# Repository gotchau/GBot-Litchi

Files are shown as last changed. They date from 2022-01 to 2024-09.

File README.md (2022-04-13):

# 3D принтер GBot Litchi

<a href="https://discord.gg/KYU2nGtZ2r" style="height: 40px !important;">Join us on Discord</a>

**⚠ Данный принтер находится в разработке. Детали могут изменится в любой момент. Скачивая и изготовливая их сейчас, вы делаете это на свой страх и риск. Промежуточный дизайн опубликован по многочисленным просьбам и для людей, которые не против принять участие в β-тесте.**

Это принтер с областью печати 180³мм³. Рама максимально универсальная и позволяет собирать принтер на нескольких кинематиках:
  * Hbot
  * CoreXY\*
  * GBot Sync\*\*
  * GBot Type A/C/D\*\*\*
  * IDEX\*\*\*\*

И сразу пару сносок:  
\* *под CoreXY детали в разработке, однако рама достаточно жесткая, **рекомендуемая кинематика — Hbot.***  
\*\* *GBot Sync — смесь HBot и Makerbot, где от Makerbot стоит пассивная ось Y, которая является синхронизатором и не допускает перекоса балки, присущего HBot'ам.*  
\*\*\* *автор собирает на GBot Type A, подробнее можно узнать тут [в этом видео про кинематики].*  
\*\*\*\* *IDEX гипотетически поддерживается, требуется растянуть раму по оси X.*  

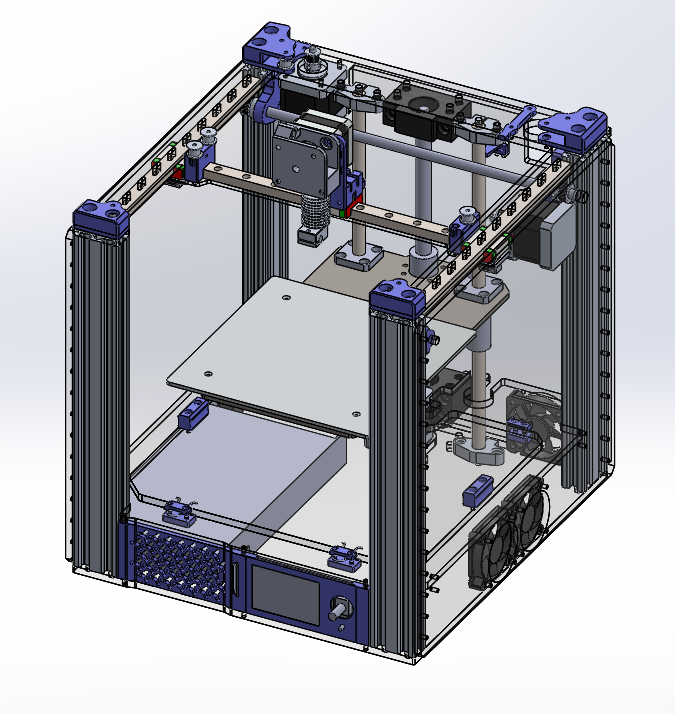
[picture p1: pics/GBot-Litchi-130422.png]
Внешний вид принтер


## Обзор конструкции
Основная часть рамы состоит из шести деталей: двух акриловых пластин и четырех профилей v-слот 2040. Профили стоят перпендикулярно и повышают жесткость и способность рамы сопротивляться скручиванию. Однако этого недостаточно, поэтому по бокам и сзади принтер тоже обшит акрилом. Боковые стенки в идеале брать толщиной 4мм (выйдет достаточно жестко и не так дорого). Автор использует везде акрил 6мм.

[в этом видео про кинематики]: https://youtu.be/pnqFbjBa5Ig

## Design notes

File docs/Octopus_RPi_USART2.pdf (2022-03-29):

### Подключение Raspberry Pi3b+ к Octopus v1.1 через USART2

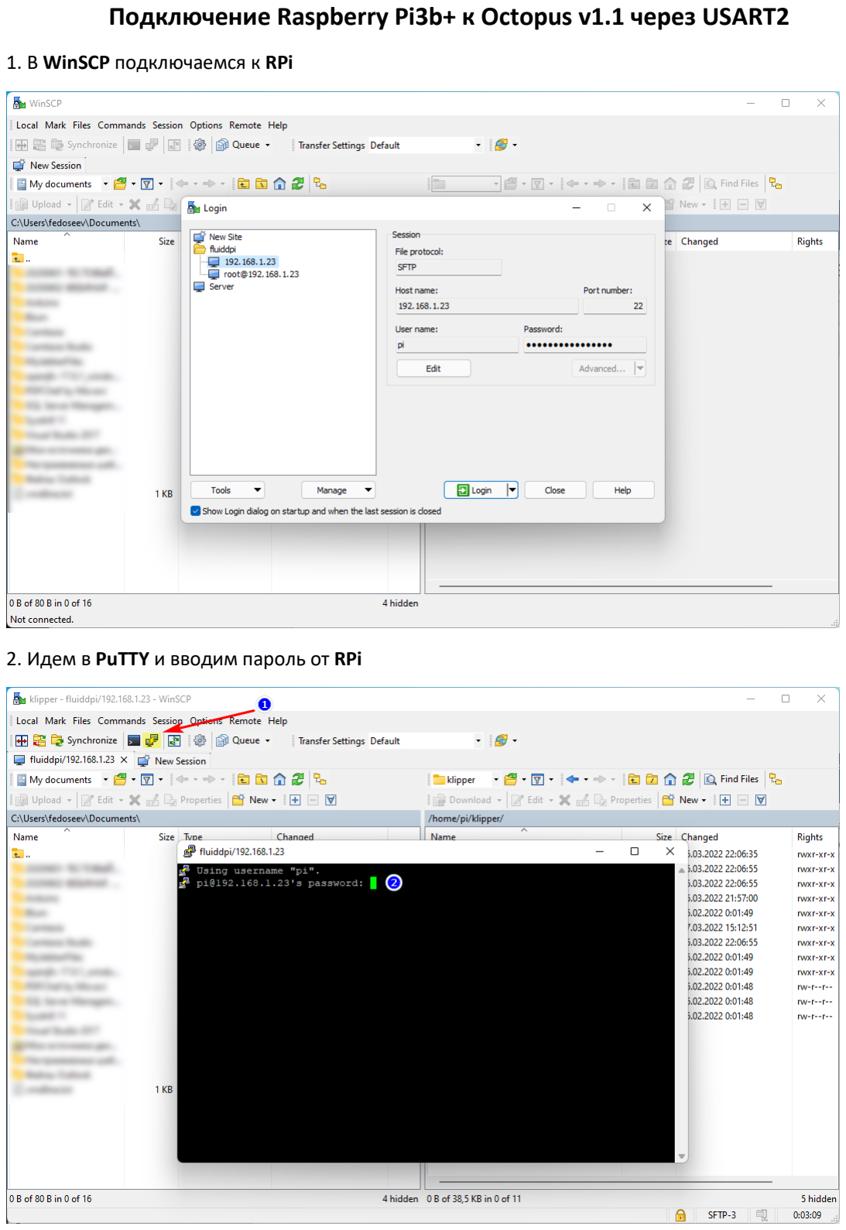
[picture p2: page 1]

1. В WinSCP подключаемся к RPi
2. Идем в PuTTY и вводим пароль от RPi

3. Переходим в папку klipper (1): cd ~/klipper и затем пишем команду make menuconfig
4. Необходимые параметры для платы BTT Octopus v1.1 (446)
a) Micro-controller Architecture (STMicroelectronics STM32)
b) Processor model (STM32F446)
c) Bootloader offset (32KiB bootloader)
d) Clock Reference (12 MHz crystal)
e) Communication interface (Serial (on USART2 PD6/PD5)) <- только для подключения через USART2
f) (250000) Baud rate for serial port

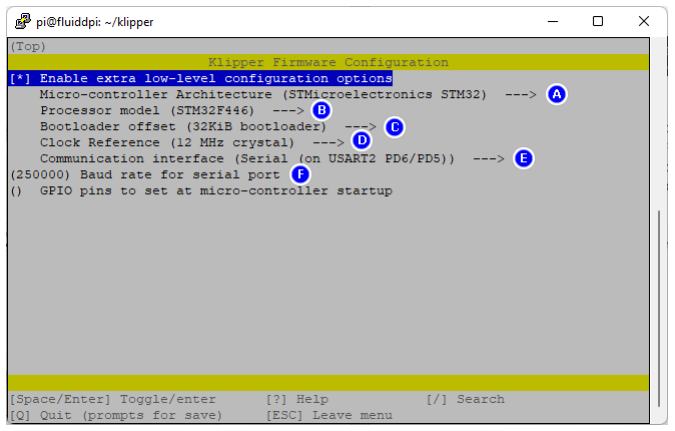
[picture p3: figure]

5. Нажимаем Q и сохраняем.
6. Пишем команду make и ждем пока создается прошивка. Файл пошивки klipper.bin можно найти в папке /home/pi/klipper/out.

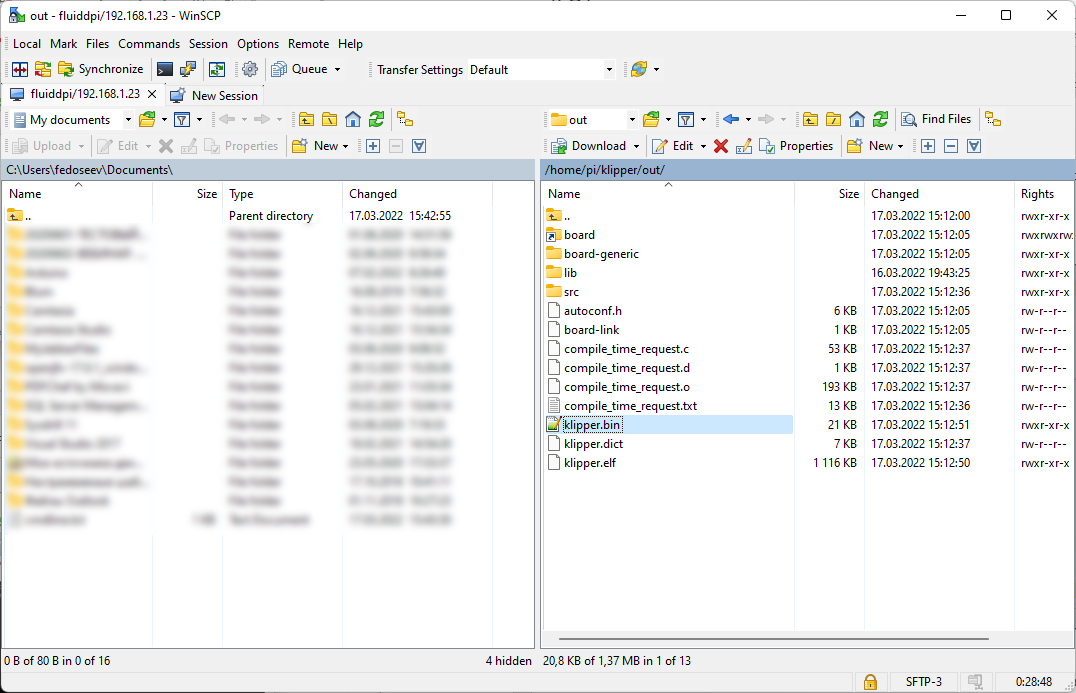
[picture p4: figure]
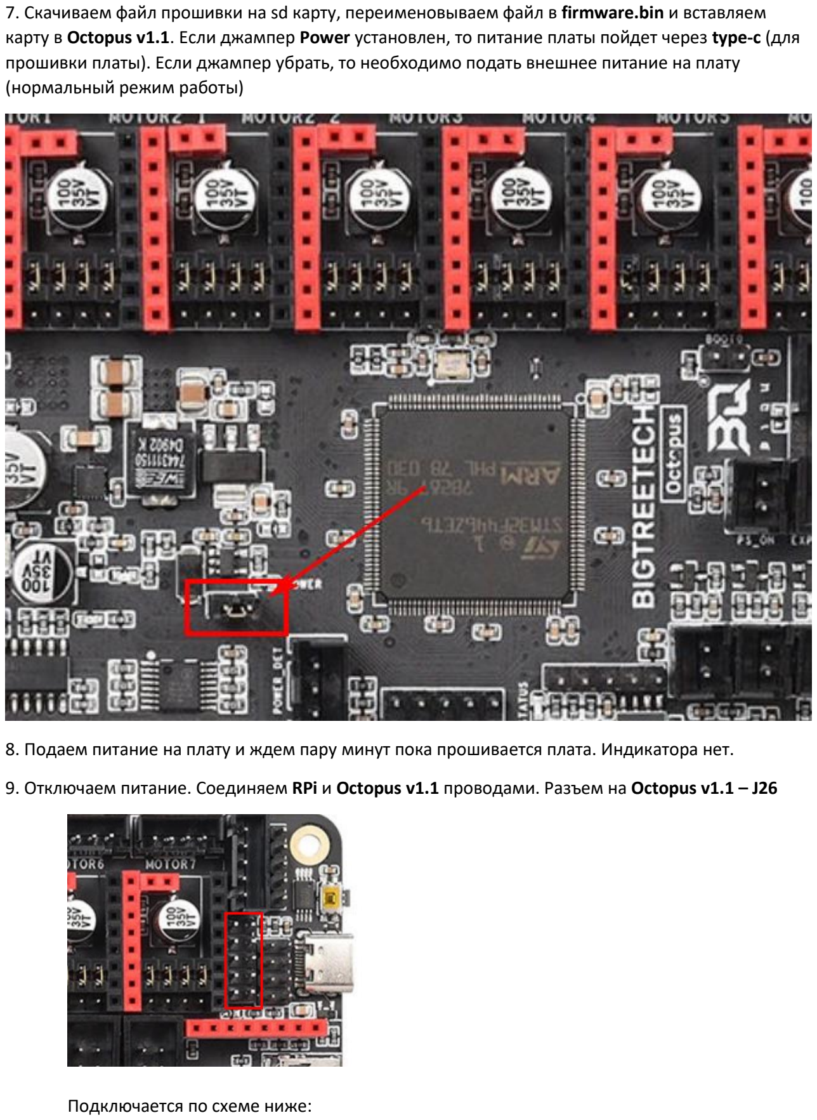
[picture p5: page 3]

7. Скачиваем файл прошивки на sd карту, переименовываем файл в firmware.bin и вставляем карту в Octopus v1.1. Если джампер Power установлен, то питание платы пойдет через type-c (для прошивки платы). Если джампер убрать, то необходимо подать внешнее питание на плату (нормальный режим работы)
8. Подаем питание на плату и ждем пару минут пока прошивается плата. Индикатора нет.
9. Отключаем питание. Соединяем RPi и Octopus v1.1 проводами. Разъем на Octopus v1.1 – J26

Подключается по схеме ниже:

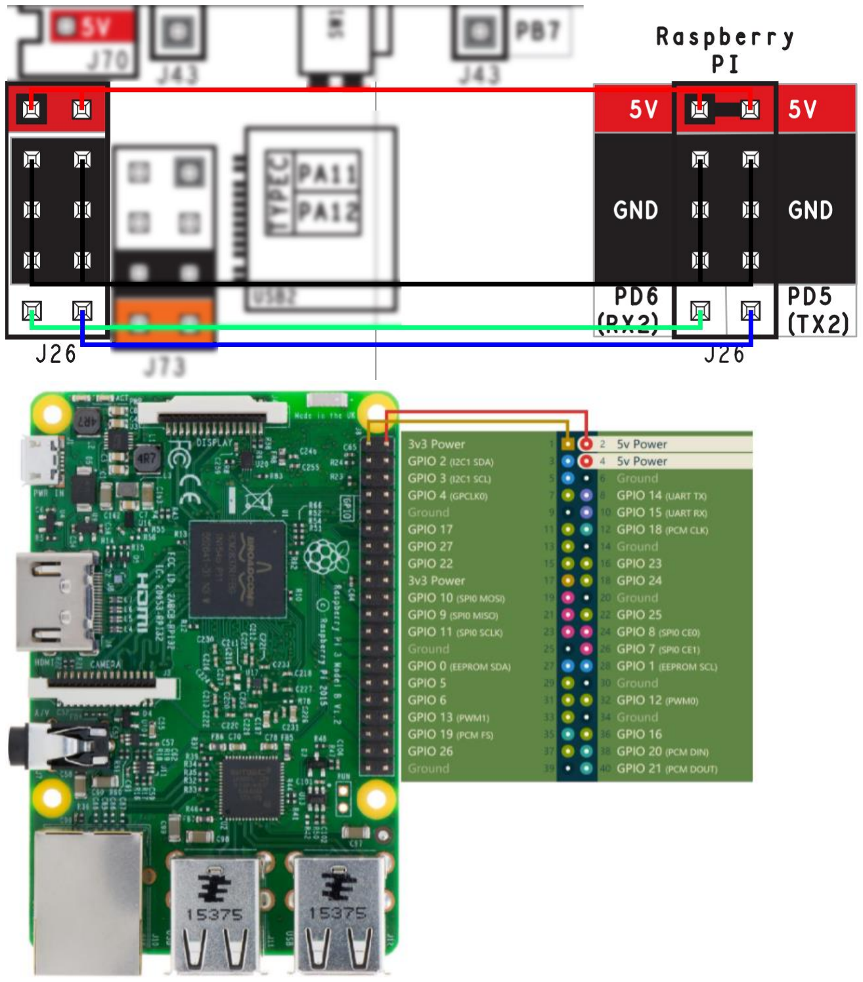
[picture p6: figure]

Плата Octopus v1.1 | RPi 3B+
5V | 5v Power
5V | 5v Power
GND | Ground
GND | Ground
PD6 (RX2) | GPIO 14 (UART TX)
PD5 (TX2) | GPIO 15 (UART RX)

Должно получиться так:

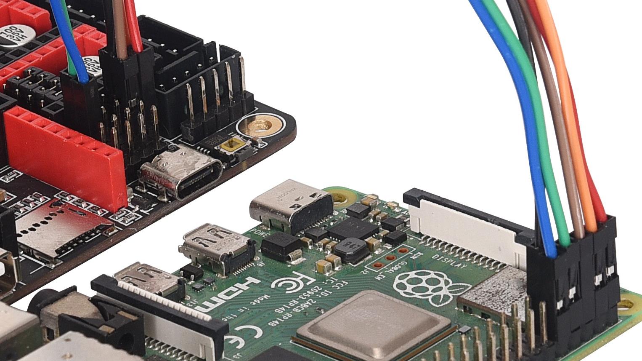
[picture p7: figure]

10. Подаем питание на Octopus (джампер Power снят, питание внешнее).
11. Заходим через WinSCP с правами root на RPi, идем сюда /boot/cmdline.txt и удаляем console=serial0,115200
12. Добавляем dtoverlay=pi3-miniuart-bt в конец файла /boot/config.txt
13. В файле конфигурации printer.cfg модифицируем раздел [mcu]

[mcu]
serial: /dev/ttyAMA0
restart_method: command
14. Перезагружаемся.

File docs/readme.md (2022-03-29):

Здесь будут публиковаться документация по принтеру:
* Основной мануал (в разработке)
* Даташиты на электронные компоненты, применяемые в принтере
* Мануалы по отдельным вариативным этапам сборки

Принять активное участие по разработке принтера можно в нашем **дискорд сервере**:  
https://discord.gg/KYU2nGtZ2r

Список файлов с пояснением:

* **A3141-2-3-4-Datasheet.pdf** -> даташит на датчик Холла A3144, применяемый в качестве концевика

* **Octopus_RPi_USART2.pdf** -> подключение RaspberryPi к Octopus  
За данную поэтапную инструкцию огромная благодарность art#9748

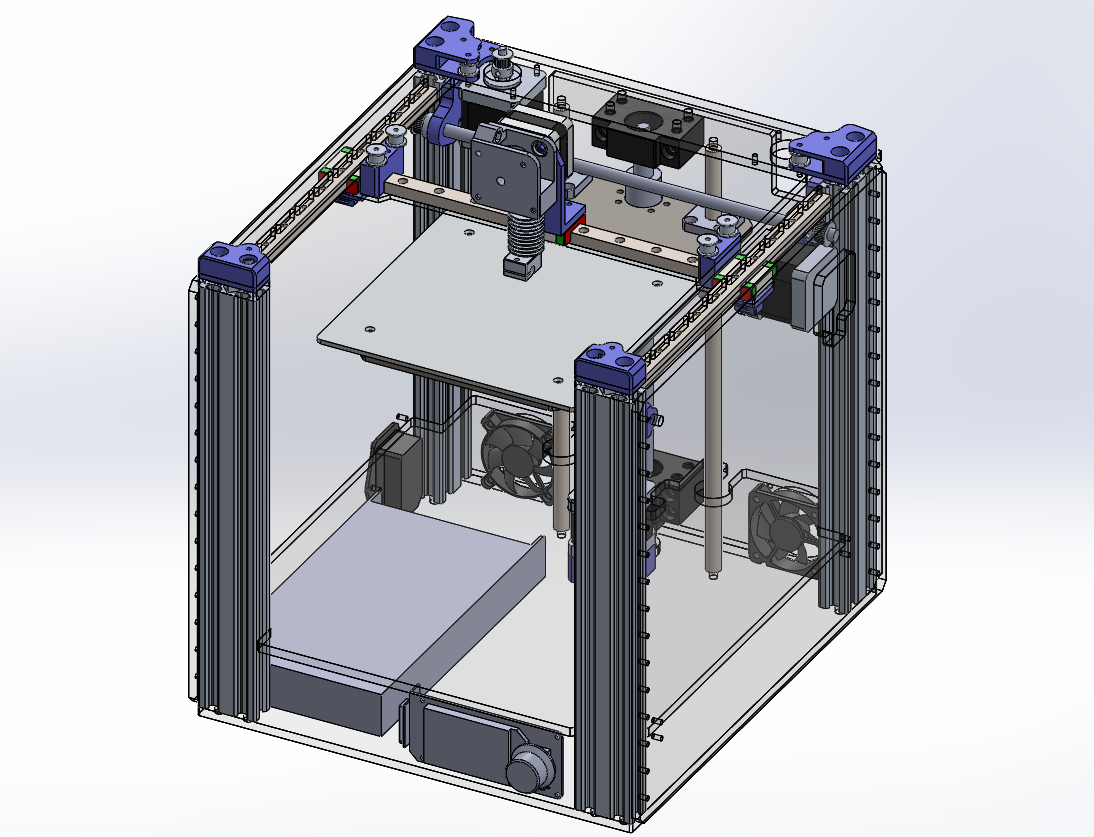
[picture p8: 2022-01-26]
pics/early-rough-design.png

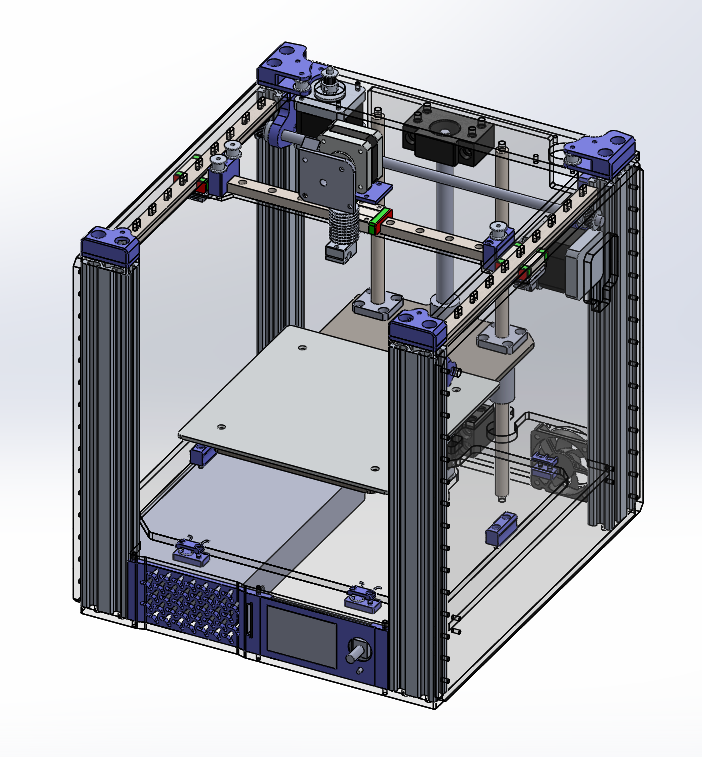
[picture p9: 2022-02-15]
pics/GBot-Litchi-150222.png

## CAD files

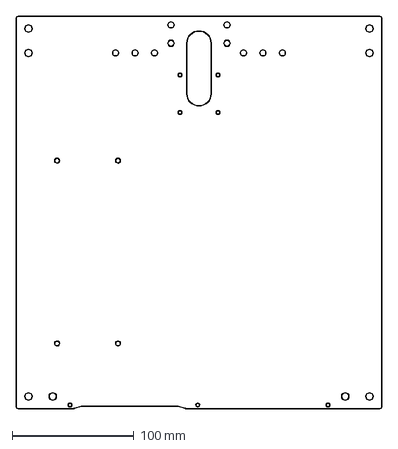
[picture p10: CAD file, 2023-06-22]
CAD/DXF/bottomPlate GBtLitchi.DXF
300.0 x 322.0 mm

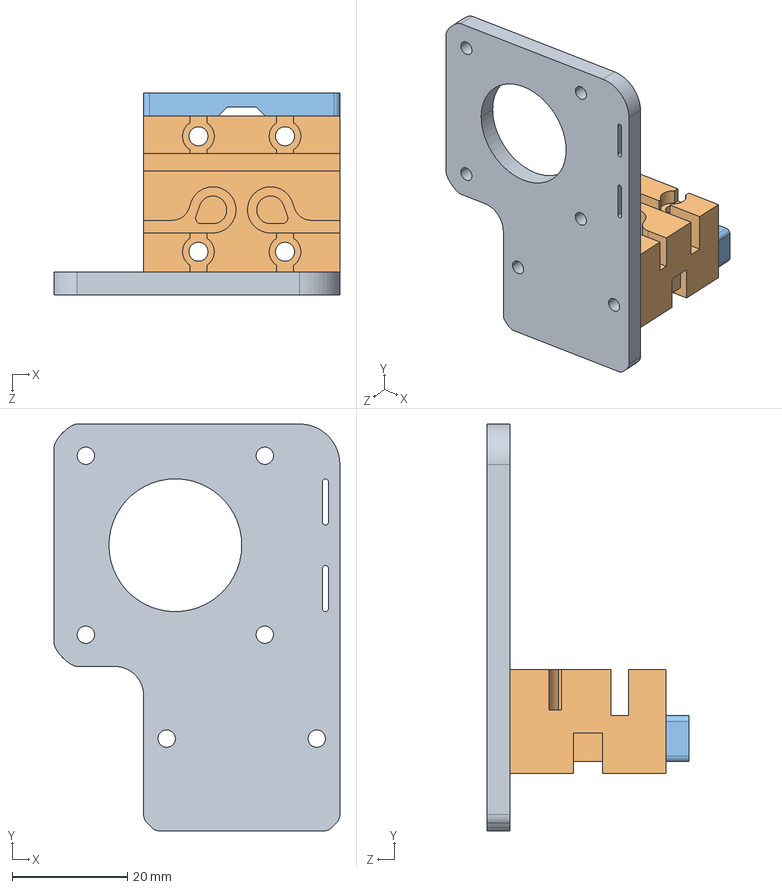
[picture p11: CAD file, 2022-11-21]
CAD/STEP/extruderMount Mk2 GBtLitchi.STEP
49.5 x 70.5 x 35.0 mm

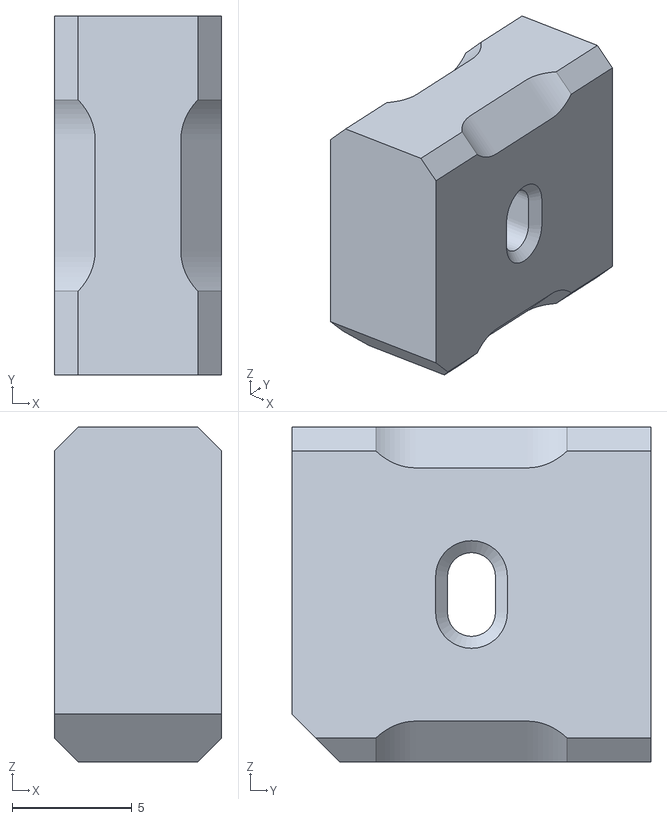
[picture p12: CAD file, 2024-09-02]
CAD/STL/zHallEndstopMount GBtLitchiMII.STL
7.00 x 15.0 x 14.0

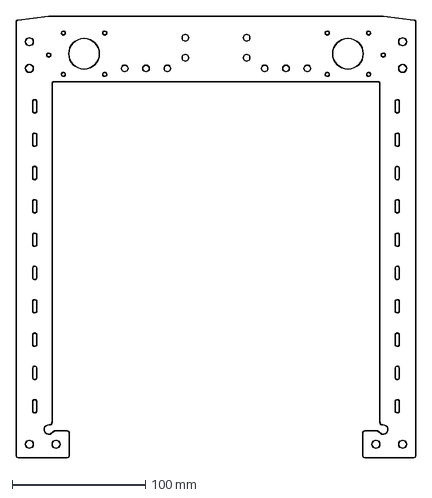
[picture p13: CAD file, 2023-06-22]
CAD/DXF/topPlate GBtLitchi.DXF
300.0 x 331.0 mm

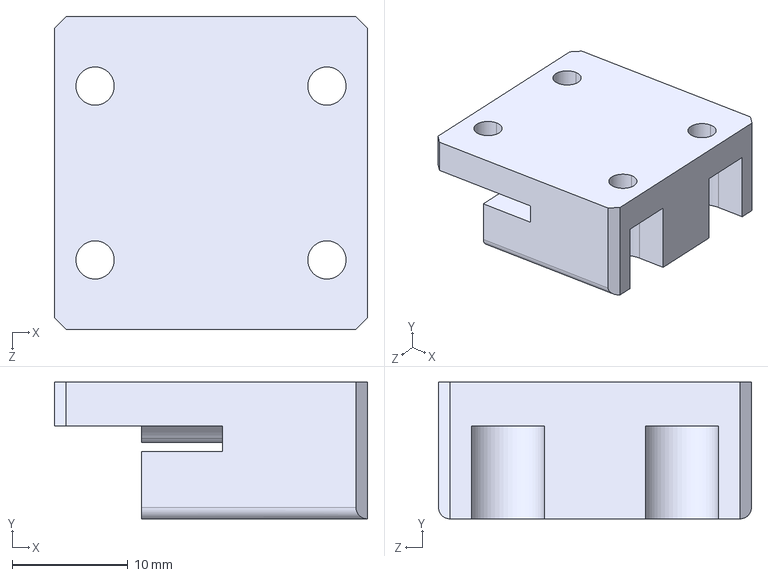
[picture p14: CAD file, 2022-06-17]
CAD/STEP/yBeltClip Mk2 T2 GBtLitchi.STEP
27.0 x 11.8 x 27.0 mm

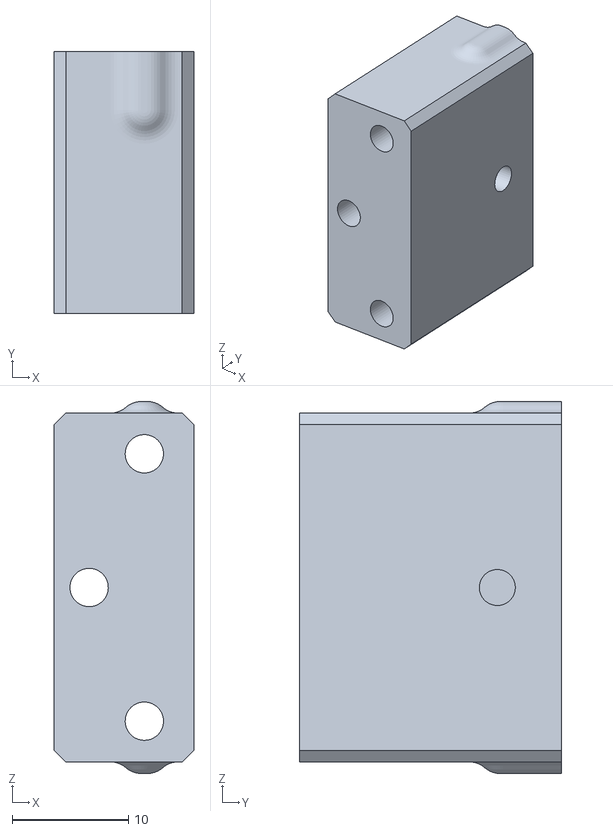
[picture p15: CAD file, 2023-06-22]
CAD/STL/rollersMount GBtLitchi.STL
12.0 x 22.5 x 32.0

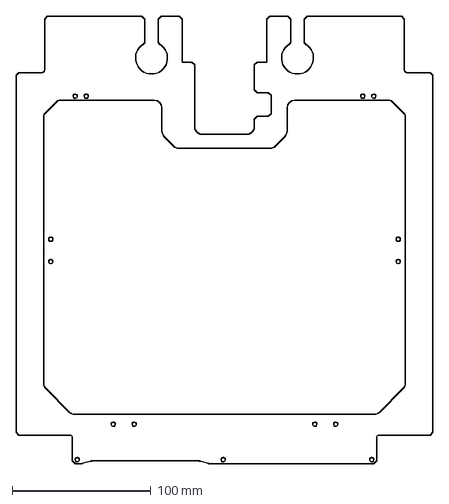
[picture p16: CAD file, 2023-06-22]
CAD/DXF/electronicsCover GBtLitchi.DXF
300.0 x 322.0 mm

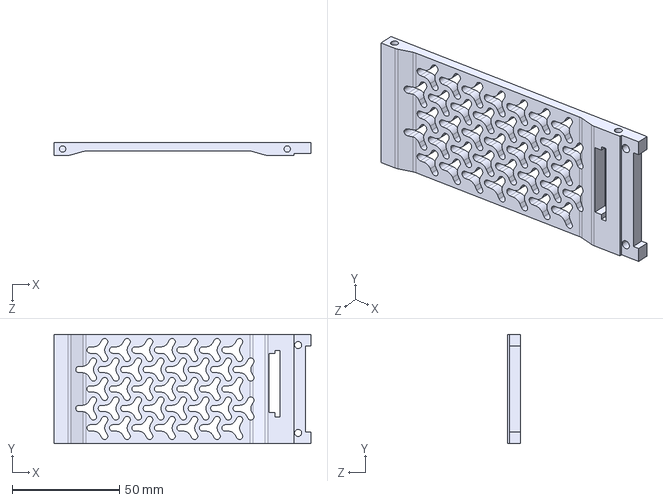
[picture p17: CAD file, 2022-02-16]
CAD/STEP/leftMini12864PanelMount GBtLitchi.STEP
120.0 x 51.0 x 6.00 mm

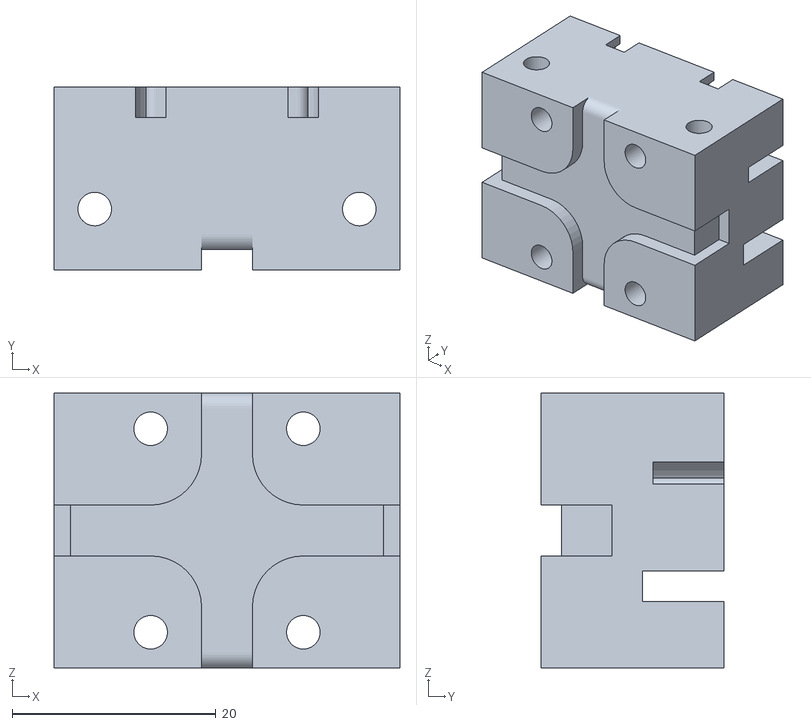
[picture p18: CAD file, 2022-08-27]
CAD/STL/extruderMount Mk2 P1 GBtLitchi.STL
34.0 x 18.0 x 27.0

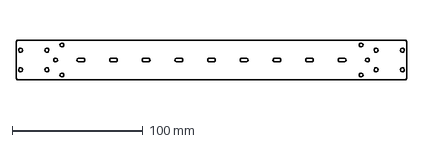
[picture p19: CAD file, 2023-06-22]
CAD/DXF/xRailSupport GBtLitchi.DXF
299.0 x 30.0 mm

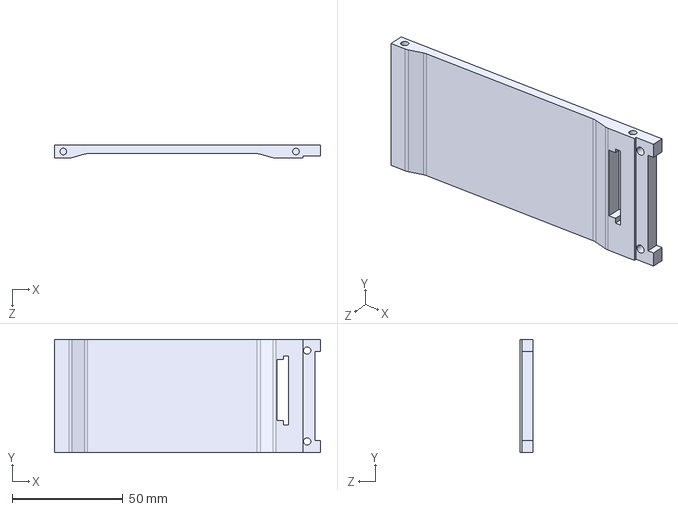
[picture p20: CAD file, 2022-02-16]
CAD/STEP/leftMini12864PanelMount Blank GBtLitchi.STEP
120.0 x 51.0 x 6.00 mm

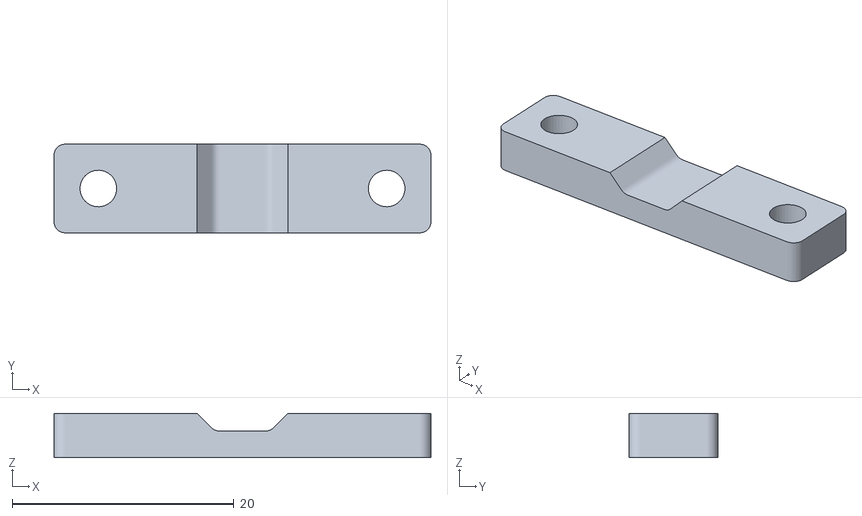
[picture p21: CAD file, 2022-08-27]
CAD/STL/extruderMount Mk2 P3 GBtLitchi.STL
34.0 x 8.00 x 4.00

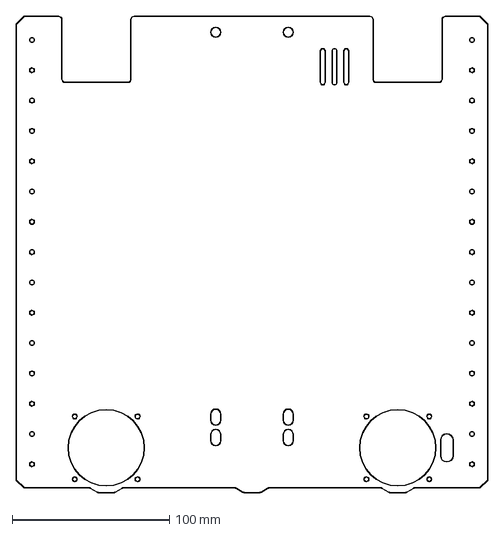
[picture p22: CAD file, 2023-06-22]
CAD/DXF/backPanel GBtLitchi.DXF
300.0 x 303.0 mm

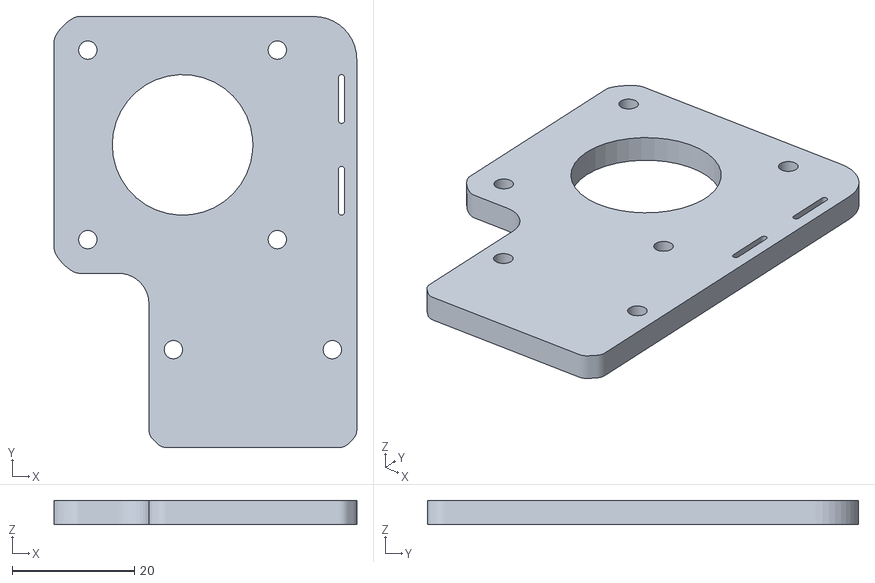
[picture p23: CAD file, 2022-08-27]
CAD/STL/extruderMount Mk2 P2 GBtLitchi.STL
49.5 x 70.5 x 4.00

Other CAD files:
CAD/DXF/leftPanel GBtLitchi.DXF
CAD/STL/stepperIdlePulleyMount I GBtLitchi.STL
CAD/DXF/rightPanel GBtLitchi.DXF
CAD/STL/hexStandoff3mm.STL
CAD/DXF/extruderMount Mk2 GBtLitchi.DXF
CAD/DXF/hotbedMount GBtLitchi.DXF
CAD/STL/extruderMount GBtLitchi.STL
CAD/STL/extruderMount II GBtLitchi.STL
CAD/STL/frontIdlePulleyMount GBtLitchi.STL
CAD/STL/frontIdlePulleyNut.STL
CAD/STL/hexStandoffRaspberry.STL
CAD/STL/idlePulleyMount I GBtLitchi.STL
CAD/STL/idlePulleyMount II GBtLitchi.STL
CAD/STL/justOneNut.STL
CAD/STL/leftMini12864PanelMount Blank GBtLitchi.STL
CAD/STL/leftMini12864PanelMount GBtLitchi.STL
CAD/STL/nutCap.STL
CAD/STL/panelProfileNutX3 sup.STL
CAD/STL/panelProfileNutX3.STL
CAD/STL/stepperIdlePulleyMount II GBtLitchi.STL
CAD/STL/yBeltClip Mk2 T2 GBtLitchi.STL
CAD/STL/yBeltClip.STL
CAD/STL/yDriveNut.STL
CAD/STL/yDriveRodMount Motor.STL
CAD/STL/yDriveRodMount.STL
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

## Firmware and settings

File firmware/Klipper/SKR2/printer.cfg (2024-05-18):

#Конфигурационный файл GBot Litchi
#Плата BTT SKR 2
#Кинематика GBot TypeA (Markforged)
#Gotchau 23.03.22

[stepper_x]
step_pin: PE2
dir_pin: PE1
enable_pin: !PE3
microsteps: 16
rotation_distance: 32
endstop_pin: ^!PC1
position_endstop: 180
position_max: 180
homing_speed: 50
homing_positive_dir: true
homing_retract_dist: 2

[stepper_y]
step_pin: PD5
dir_pin: PD4
enable_pin: !PD6
microsteps: 16
rotation_distance: 40
endstop_pin: ^!PC3
position_endstop: 180
position_max: 180
homing_speed: 50
#homing_positive_dir: true
homing_retract_dist: 2

[stepper_z]
step_pin: PA15
dir_pin: !PA8
enable_pin: !PD1
microsteps: 16
rotation_distance: 4
endstop_pin: ^!PC0
position_min: 0.0
position_max: 166.5
#position_endstop = 0
homing_speed: 10

[extruder]
step_pin: PD15
dir_pin: PD14
enable_pin: !PC7
microsteps: 16
rotation_distance: 25.2 #3.14*8
gear_ratio: 66:22
nozzle_diameter: 0.400
filament_diameter: 1.750
heater_pin: PB3
sensor_type: EPCOS 100K B57560G104F
sensor_pin: PA2
control = pid
pid_kp = 28.904
pid_ki = 1.966
pid_kd = 106.221
min_temp: 0
max_temp: 250
min_extrude_temp: 0
max_extrude_only_distance: 300

[heater_bed]
heater_pin: PD7
sensor_type: Generic 3950
sensor_pin: PA1
max_power: 0.7
control = pid
pid_kp = 51.822
pid_ki = 0.715
pid_kd = 938.625
pwm_cycle_time: 0.050
min_temp: 0
max_temp: 130

#When 12V fan connected to 24V power supply
#the max_power should not exceed 0.5
[fan]
pin: PB5
max_power: 0.5

[heater_fan extruder_fan]
pin: PB6

[controller_fan enclosure_fan]
pin: PB7
max_power: 0.5

[temperature_sensor host]
sensor_type: temperature_host

#MCU temperature
#[temperature_sensor mcu]
#sensor_type: temperature_mcu

# Due to BTT implementing a Marlin-specific safety feature,
# "anti-reversal stepper protection", this pin needs pulling
# high to pass power to stepper drivers and most FETs
[output_pin motor_power]
pin: PC13
value: 1

[mcu]
#serial: /dev/serial/by-id/usb-Klipper_stm32f429xx_2F004B001550305031353020-if00
serial: /dev/ttyAMA0
#baud: 250000
restart_method: command

[printer]
kinematics: hybrid_corexy
max_velocity: 300
max_accel: 5000
max_accel_to_decel: 3000
square_corner_velocity:5
max_z_velocity: 25
max_z_accel: 100

#[homing_override]
#gcode:
#    G28 X0
#    G28 Y0
#    G28 Z0

########################################
# EXP1 / EXP2 (display) pins
########################################
[board_pins]
aliases:
    # EXP1 header
    EXP1_1=PC5, EXP1_3=PB1, EXP1_5=PE10, EXP1_7=PE12, EXP1_9=<GND>,
    EXP1_2=PB0, EXP1_4=PE9, EXP1_6=PE11, EXP1_8=PE13, EXP1_10=<5V>,
    # EXP2 header
    EXP2_1=PA6, EXP2_3=PE7, EXP2_5=PB2, EXP2_7=PC4,   EXP2_9=<GND>,
    EXP2_2=PA5, EXP2_4=PA4, EXP2_6=PA7, EXP2_8=<RST>, EXP2_10=<NC>


######################################################################
# Fysetc Mini 12864Panel v2.1 (with neopixel backlight leds)
######################################################################
[display]
lcd_type: uc1701
cs_pin: EXP1_3
a0_pin: EXP1_4
rst_pin: EXP1_5
contrast: 63
encoder_pins: ^EXP2_5, ^EXP2_3
click_pin: ^!EXP1_2
spi_software_miso_pin: EXP2_1
spi_software_mosi_pin: EXP2_6
spi_software_sclk_pin: EXP2_2

[output_pin beeper]
pin: EXP1_1
pwm: True
value: 0
shutdown_value: 0
cycle_time: 0.0002

[neopixel fysetc_mini12864]
pin: EXP1_6
chain_count: 3
color_order: RGB
initial_RED: 0.6
initial_GREEN: 0.0
initial_BLUE: 1.0

########################################
# TMC2208 configuration
########################################
[tmc2208 stepper_x]
uart_pin: PE0
run_current: 1.000
interpolate: True
stealthchop_threshold: 300

[tmc2208 stepper_y]
uart_pin: PD3
run_current: 1.000
interpolate: True
stealthchop_threshold: 300

[tmc2208 stepper_z]
uart_pin: PD0
run_current: 0.700
interpolate: True
stealthchop_threshold: 300

[tmc2208 extruder]
uart_pin: PC6
run_current: 0.700
interpolate: True
stealthchop_threshold: 300

[pause_resume]

[gcode_macro CANCEL_PRINT]
description: Cancel the actual running print
rename_existing: CANCEL_PRINT_BASE
gcode:
  TURN_OFF_HEATERS
  CANCEL_PRINT_BASE

[display_status]

[virtual_sdcard]
path: ~/gcode_files

#[force_move]
#enable_force_move: true
#   Set to true to enable FORCE_MOVE and SET_KINEMATIC_POSITION
#   extended G-Code commands. The default is false.

#*# <---------------------- SAVE_CONFIG ---------------------->
#*# DO NOT EDIT THIS BLOCK OR BELOW. The contents are auto-generated.
#*#
#*# [stepper_z]
#*# position_endstop = 0.295
